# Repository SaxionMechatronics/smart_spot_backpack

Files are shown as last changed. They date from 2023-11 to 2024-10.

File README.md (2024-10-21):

# SMART SPOT Backpack

<p align="center" width="100%">
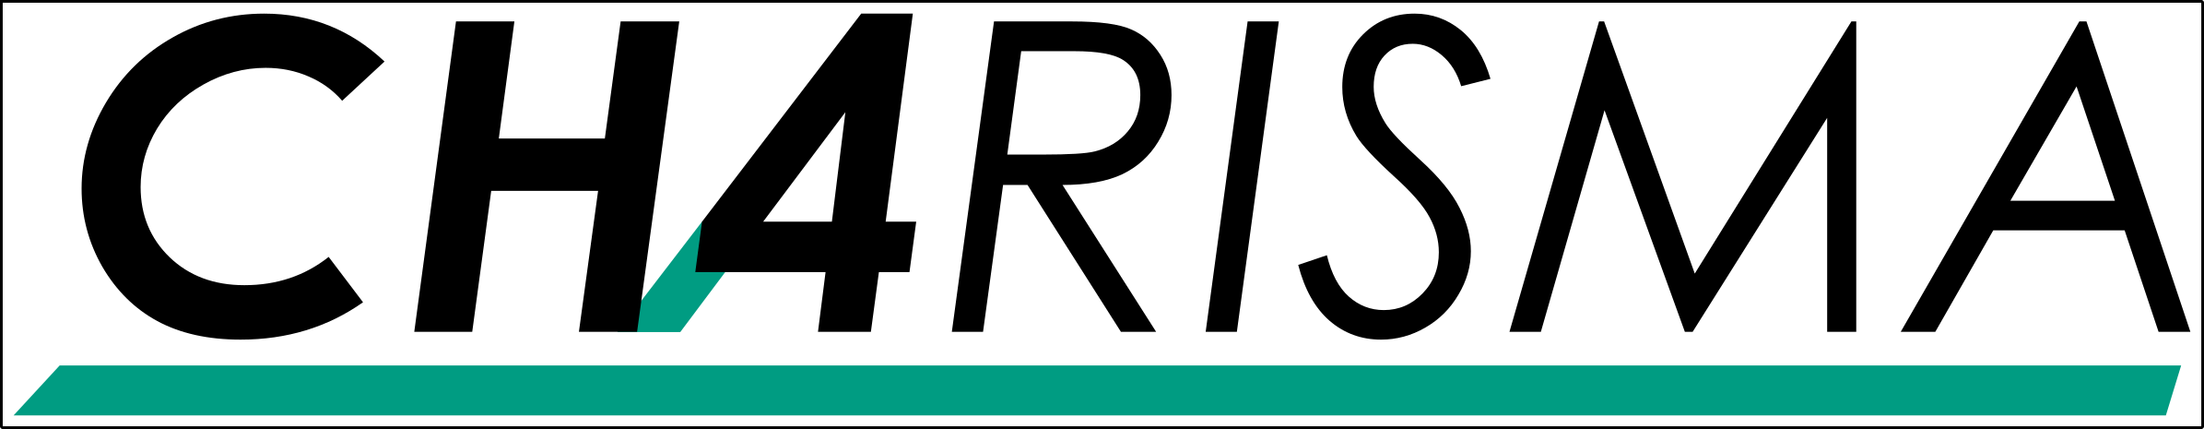
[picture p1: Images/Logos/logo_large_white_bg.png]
  
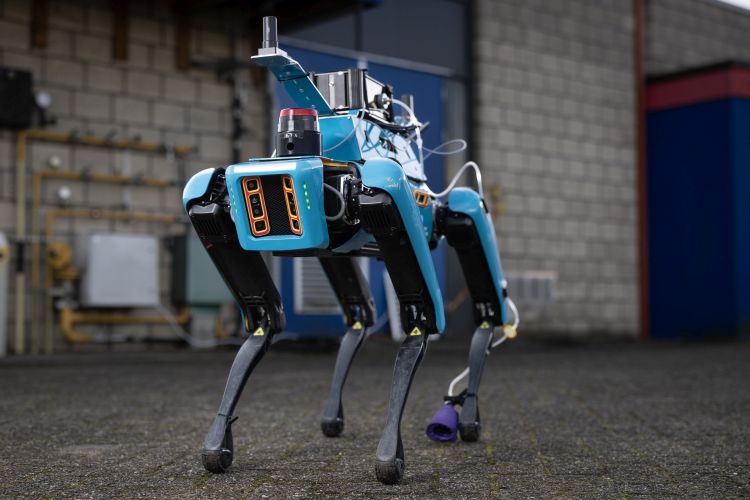
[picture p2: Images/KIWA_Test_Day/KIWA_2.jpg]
    
    <br>
    <em>SMART SPOT backpack being used in the CHARISMA project.</em>
</p>

This repository contains the SolidWorks files and documentation for the SMART SPOT Backpack: a backpack that has been developed for the Boston Dynamics robot [SPOT](https://bostondynamics.com/products/spot/) as part of the CHARISMA project of the [Smart Mechatronics And RoboTics (SMART) Research Group](https://www.saxion.edu/business-and-research/research/smart-industry/mechatronics) of the Saxion University of Applied Sciences. 

# Documentation
  * [A Word On Documentation](/Documentation/00-title.md)
  * [Context](/Documentation/01-context.md)
  * [Functional Overview](/Documentation/02-functional-overview.md)
  * [Quality Attributes](/Documentation/03-quality-attributes.md)
  * [Constraints](/Documentation/04-constraints.md)
  * [Requirements](/Documentation/xx-requirements.md)
  * [Principles](/Documentation/05-principles.md)
  * [Implementation](/Documentation/07-Implementation.md)
    * List of Parts 
    * Power Distribution
  * [Instructions](/Documentation/8-instructions.md)
    * [Manufacturing Instructions](/Documentation/8.1-manufacturing-instructions.md)
    * [Assembly Instructions](/Documentation/8.2-assembly-instructions.md)
    * [Mounting Instructions](/Documentation/8.3-mounting-instructions.md)
  * [Development Environment](/Documentation/12-development-environment.md)
  * [Support and Contributions](/Documentation/11-support-and-contributions.md)
  * [Architecture Decision Records](/Documentation/11-decision-log.md)
  * [Suggested Changes](/Documentation/12-Suggested-Changes.md)

# Specifications

| Parameter | Backpack V2.0.0 | 
| --- | --- |
| Weight | 3 kg |
| Dimensions | 20 x 40 x 10.5 cm|
| Material | Aluminium Sheet Metal |
| Voltage Outputs | 5, 12, 24 V (M12 Connectors) |
| Media Connectors | 4x USB 3.0, HDMI, Ethernet |
| On-board PC | VECOW SPC-7000|

# Directory Structure

```md
SPOT Backpack Repository                
├── CAD 
│   ├── 3D Drawings                     # .SLDPRT and .step files used in the assembly
|   |   ├── 3D Print Components
|   |   ├── Sheet Metal Components
|   |   ├── Other Components
│   |   └── Backpack Assembly.SLDASM    # Main assembly
│   └── Production Drawings             # Parts to be produced
|       ├── 3D Print Components         # .3MF files
|       └── Sheet Metal Components      # .step files for SOPHIA
├── Documentation
├── Images
└── Other Files                         
```

<p align="center">
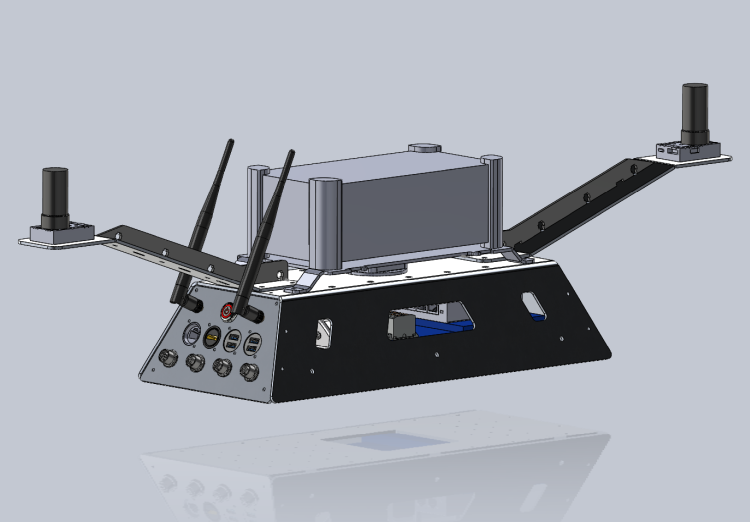
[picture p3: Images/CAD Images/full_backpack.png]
    
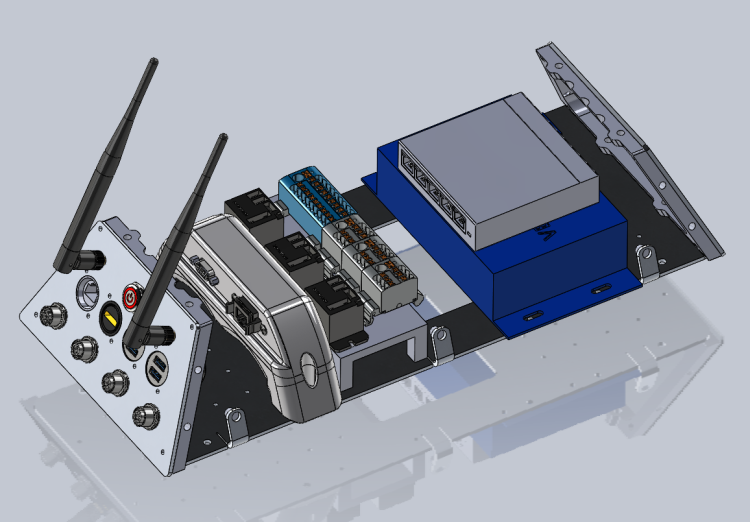
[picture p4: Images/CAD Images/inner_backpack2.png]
    
    <p align="center"><i>Solidworks assembly of the SMART SPOT Backpack.</i></p>
</p>

<p align="center" width="100%">
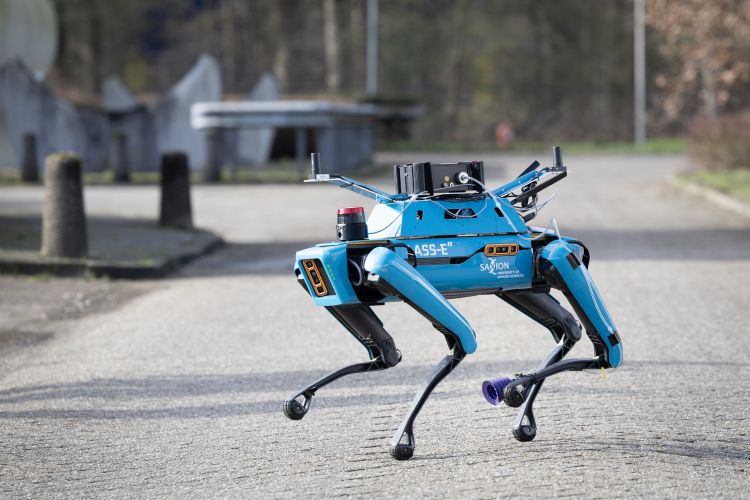
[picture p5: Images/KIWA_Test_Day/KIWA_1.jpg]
    
    <br>
    <em>SMART SPOT Backpack in action.</em>
</p>

## License
This project is released under the [CERN OHL v2 Weakly Reciprocal](https://choosealicense.com/licenses/cern-ohl-w-2.0/) license. Feel free to use, modify, and distribute the hardware designs in accordance with the terms of the license.

## Acknowledgments
This work from the SMART research group at Saxion University of Applied Sciences was supported by the Alliander Research Center for Digital Technologies and TechForFuture.

<p align="center" width="100">
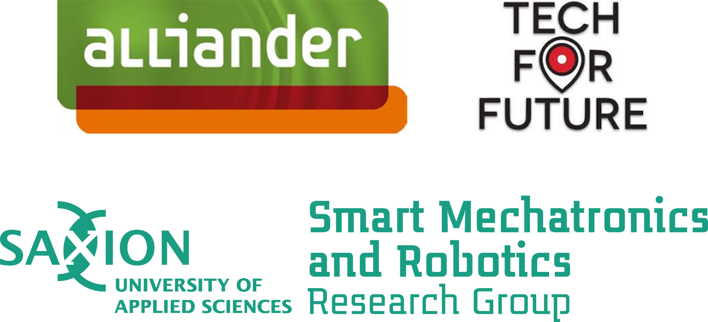
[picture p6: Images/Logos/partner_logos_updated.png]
    
</p>

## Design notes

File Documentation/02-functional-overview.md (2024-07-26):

## Functional Overview

This section gives a functional overview of the system as shown in figure 1: 

<p align="center" width="100%">
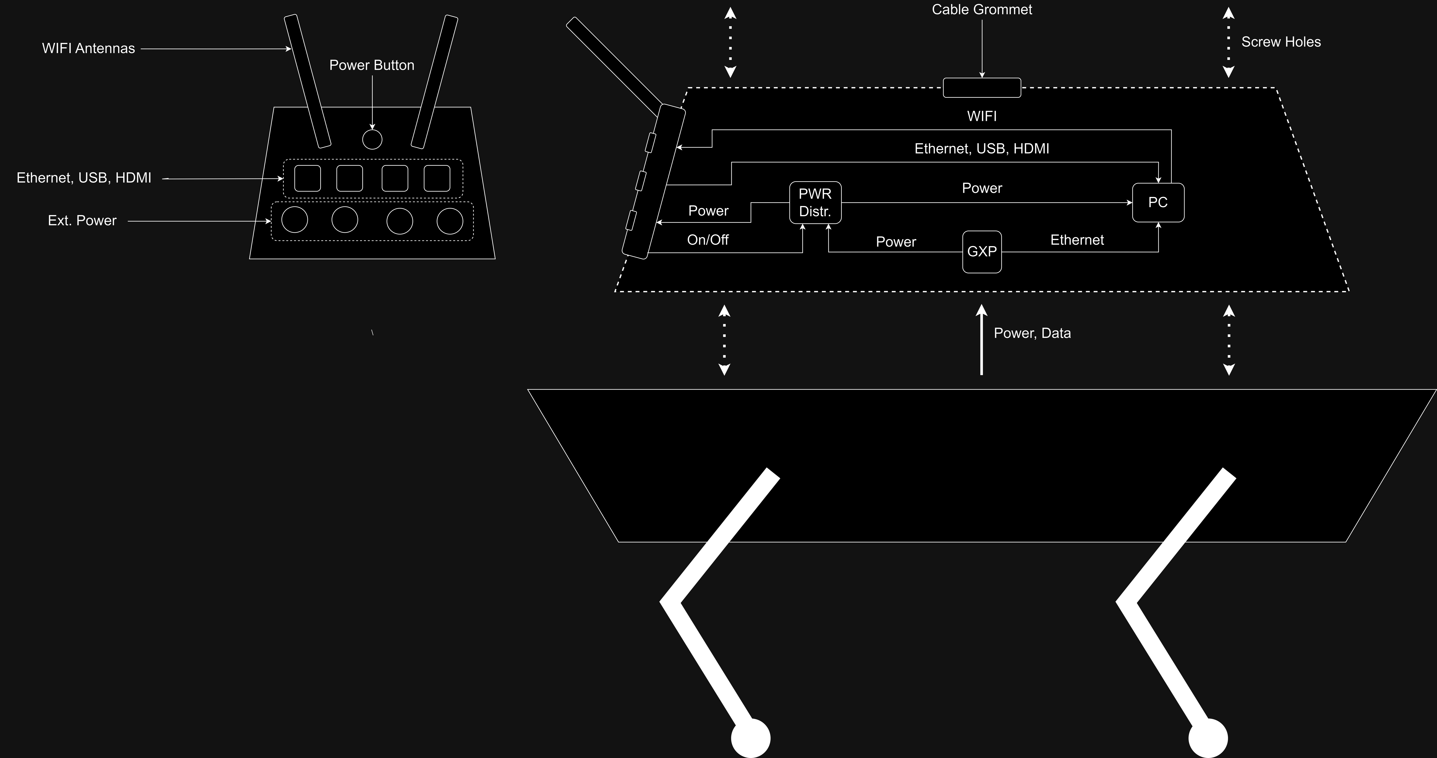
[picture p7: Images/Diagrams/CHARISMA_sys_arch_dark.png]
    
    <br>
    <em>Figure 1: Functional overview of the SPOT Backpack.</em>
</p>

In this diagram you can see that:
- The [General Expansion Payload (GXP)](https://support.bostondynamics.com/s/article/Spot-General-Expansion-Payload-GXP) provides power and data communication from SPOT 
- The power button bridges the power from the GXP to the power distribution
- Power is distributed via the power distribution (PWR Distr.) to the PC and to the interface panel
- The PC provides WIFI via 2 WIFI antennas
- The interface panel has various connectors that allow development with the on-board PC
- The top surface of the backpack includes a cable grommet and an array of screw holes

For a more in-depth electrical diagram, please see the [implementation](/Documentation/07-Implementation.md) section.

Below you can see a 3D version of the Backpack in SolidWorks (without any add-on components):

<p align="center">
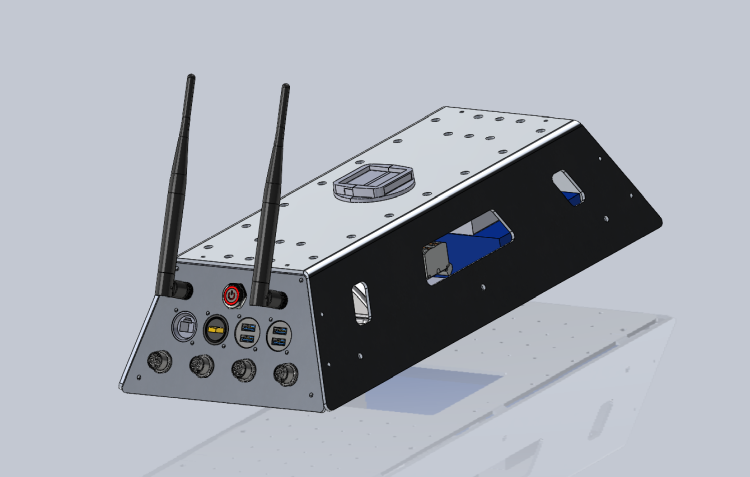
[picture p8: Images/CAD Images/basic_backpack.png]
    
    
    <p align="center"><i>SolidWorks assembly of the SMART SPOT Backpack.</i></p>
</p>

***

In the next section you can read about the key quality attributes that the system should satisfy.

> ➡️ [Next: Quality Attributes](./03-quality-attributes.md)

> ⬅️ [Previous: Context](./01-context.md)

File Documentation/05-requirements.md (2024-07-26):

## Requirements

This section describes the functional and technical requirements for the SPOT backpack. Requirements have been written based on [EARS](https://www.researchgate.net/publication/224079416_Easy_approach_to_requirements_syntax_EARS) and have been assigned a priority according to [MoSCoW](https://en.wikipedia.org/wiki/MoSCoW_method). 

*Keep in mind that these requirements have been written in context of the CHARISMA project.*

### Functional requirements

| Number | Requirement | Rationale | Priority |
| --- | --- | --- | --- |
| FR0101 | During normal operation of SPOT (i.e. walking, crouching, sitting, posing, walking stairs), the backpack shall not interfere with the motion of the robot. | We want a reliable backpack that does not interrupt basic operations of SPOT. | M | 
| FR0102 | When changing the battery while SPOT is laying on its side, the backpack shall not interfere. | If we change the battery, spot needs to be rolled over or on the side in order to access it. | M | 

### Technical requirements

#### Electric and electronic design

| Number | Requirement | Rationale | Priority |
| --- | --- | --- | --- |
| TR0101 | The backpack shall have clearly labelled cabling with rated voltages and current. | For maintenance reasons, it should be easy to understand the electrical wiring from just looking at it. | M | 
| TR0102 | The backpack shall provide one 24V, 12V and 5V external power connection each. | The bag pack should be able to cater the needs of various projects and their respective peripherals. | M | 
| TR0103 | The backpack shall provide different, standardized connectors for its external power connections that are labelled with rated voltages and current. | For safety reasons. For example, it should not be possible to connect a 5V to a 24V connection by accident. | M | 
| TR0104 | The backpack shall provide two WIFI antennas, one ethernet, one HDMI and four USB connections that are interfaced with its PC. | We want to easily develop on the PC of the bag pack. | M | 
| TR0105 | The backpack shall provide one power button that turns on/off its internals. | We want to power the PC and its peripherals only when needed. | M | 
| TR0106 | The power distribution of the backpack shall reserve 40W for the PC. | External devices that are powered via the 5V,12V or 24V connections should not be able to draw enough current to cut out the power to PC. The PC uses a maximum of 33.5W at peak conditions. | M | 

#### Mechanical design

| Number | Requirement | Rationale | Priority |
| --- | --- | --- | --- |
| TR0201 | The GNSS sensors of shall be located at the highest points of the backpack and not be occluded by any objects of the backpack. | Occlusions to the sky and reflections will disturb sensor readings. By placing the GNSS sensors at the highest point, we will get the best possible signal. | M | 
| TR0202 | The bag pack shall allow for a minimum distance of 80cm between the GNSS sensors. | There needs to be sufficient distance between the sensors to accurately determine the heading of the robot. | M | 
| TR0203 | The weight of the backpack shall be lower than 14.8 Kg where lower is better. | This is the maximum payload of SPOT. Reduced payload leads to reduced power consumption and thus longer operation times. | M | 
| TR0204 | The width of the backpack shall be at most 19 cm. | When the robot is not powered or walking stairs, the robot’s legs may move into the designated design space | M | 
| TR0205 | The length of the backpack shall be at most 85 cm. | Longer payloads will reduce maneuverability. | M | 
| TR0206 | The backpack shall have an IP rating of 0 where higher is better. | The backpack is built for research purposes only, it is therefore not required to have a higher IP rating. | M | 
| TR0207 | The backpack shall be made out of aluminum sheet metal. | Sheet metal parts are relative sturdy, cheap and easy to design. Additionally, they are easy to modify if needed  (e.g. drilling holes, filing). | S | 
| TR0208 | The backpack shall have only have screw holes with insert nuts (e.g. rivets nuts, heat inserts) on its outer shell. | 1) User friendliness: A user should be able to (un)-screw any object located on outer shell as easy as possible. 2) Reliability: The threading of tapped holes may deteriorate over time with repeated (un-)screwing. | S | 
| TR0209 | When (un-)mounting,  backpack shall require one tool, and two assembly steps. | User friendliness. It should be easy to (un)-mount the backpack to facilitate switching between different projects if needed. | S | 
| TR0210 | The  backpack shall require one disassembly step to access its internals. | Debugging and maintenance purposes. | S | 
| TR0211 | The backpack shall have only 3 and 5 mm screw holes. | This is to prevent confusion between screw hole sizes during assembly | S | 

***

In the next section you can read about the principles that have been used to design and build the backpack. 

> ➡️ [Next: Principles](./06-principles.md)

> ⬅️ [Previous: Constraints](./04-constraints.md)

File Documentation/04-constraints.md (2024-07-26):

## Constraints

This section states the constraints that affect the design of the backpack. The constraints and images w.r.t to SPOT are taken from the [Payload Developer Guide](https://dev.bostondynamics.com/docs/payload/payload_configuration_requirements.html) by Boston Dynamics and where applicable, further elaborated on.

Constraints include: 
- Mounting Surface
- Weight
- Dimensions
- Electrical Power and Data Interface to SPOT
- Manufacturing Guidelines of Sheet Metal Parts 

## Mounting Surface
The only mounting surface that SPOT provides are aluminum rails that are located along the left and right edges of the body. The rails accept T-slot nuts such as Misumi HNTR5-5. Mounting screws should not project more than 6.3mm below the top surface of the mounting rail.

<p align="center" width="100%">
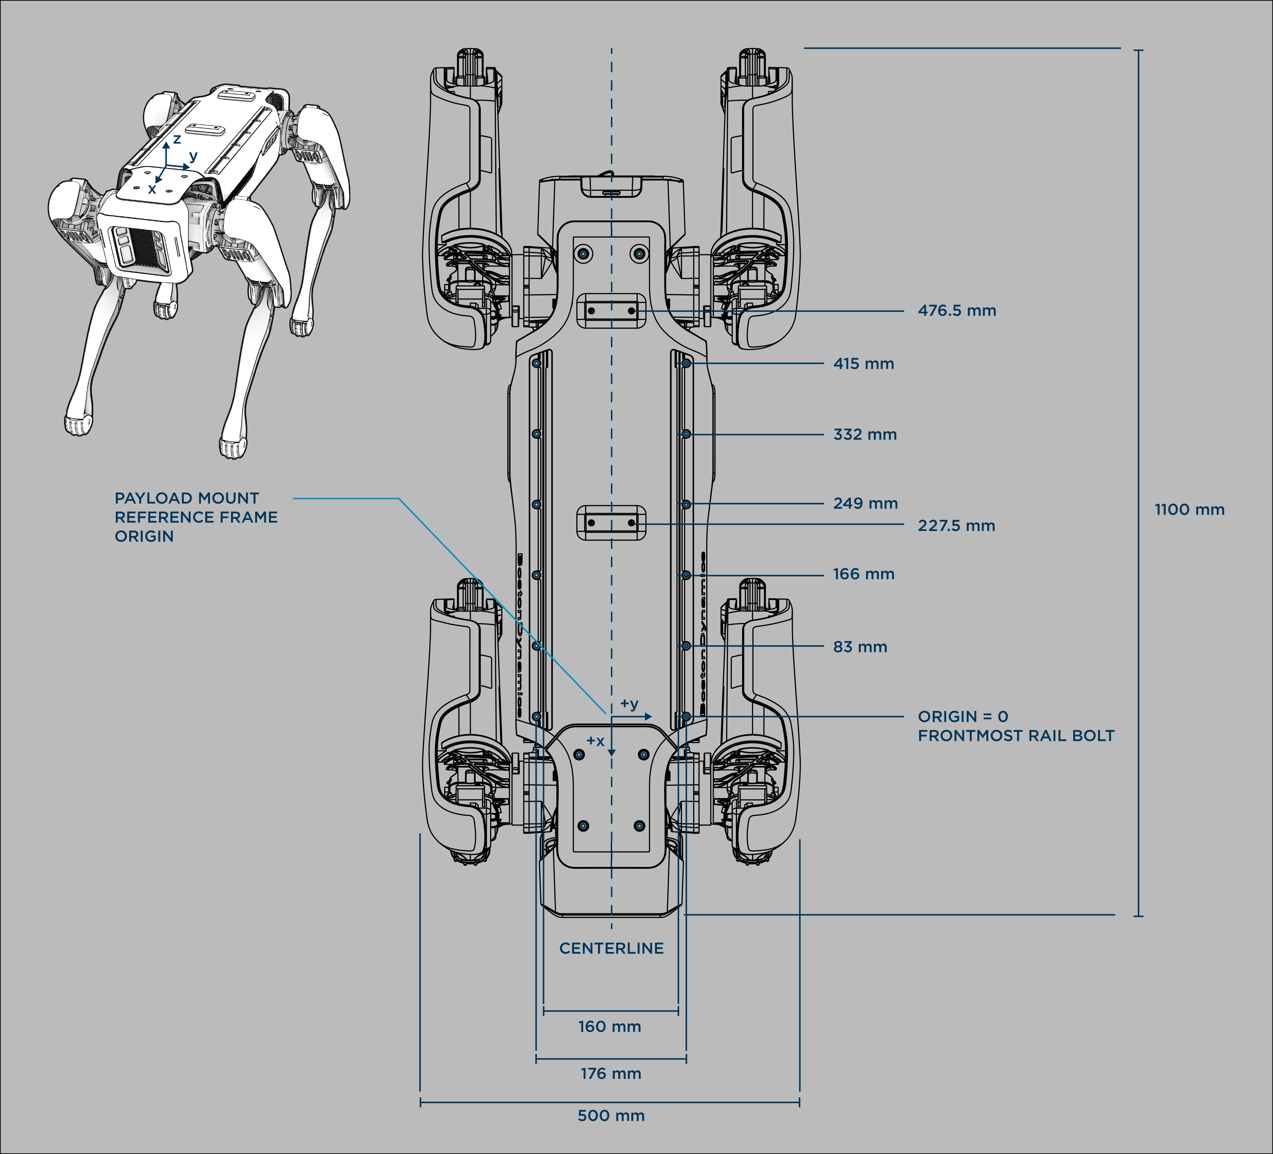
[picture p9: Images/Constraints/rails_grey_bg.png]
    
    <br>
    <em>Aluminum rails for mounting.</em>
</p>

<p align="center" width="100%">
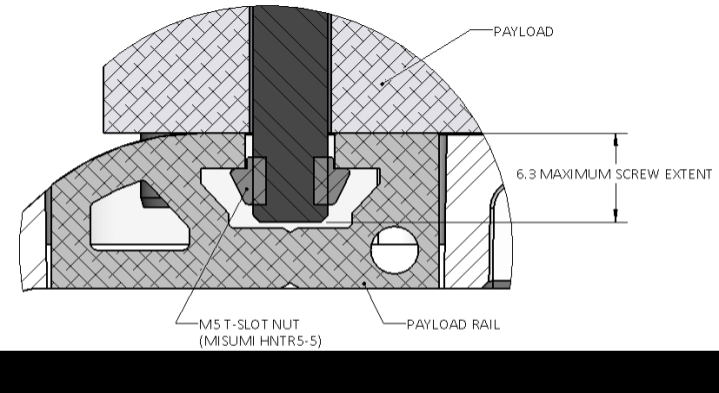
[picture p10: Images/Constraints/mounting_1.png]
    
    <br>
    <em>Mounting rail keying pin specifications in mm.</em>
</p>

## Payload Weight

SPOT has a maximum payload of 14.8 kg. Additionally, the weight of payload will also affect SPOT's battery consumption.
Furthermore, Spot can better handle payload mass if the combined center of mass lies between the front and rear hips. Spot will be more agile and less likely to fall if the total payload mass is centered on the middle of the robot.

## Payload Width
 
The maximum recommended width by Boston Dynamics for a body-mounted payload is 190mm. Wider payloads will result in reduced overall mobility and significant interference with the legs. 
For instance, SPOT's legs may shoot up when walking stairs or when self-righting.
One should thus avoid interference with the robot’s legs as shown below by avoiding the areas immediately adjacent to the robot’s hips.

<p align="center" width="100%">
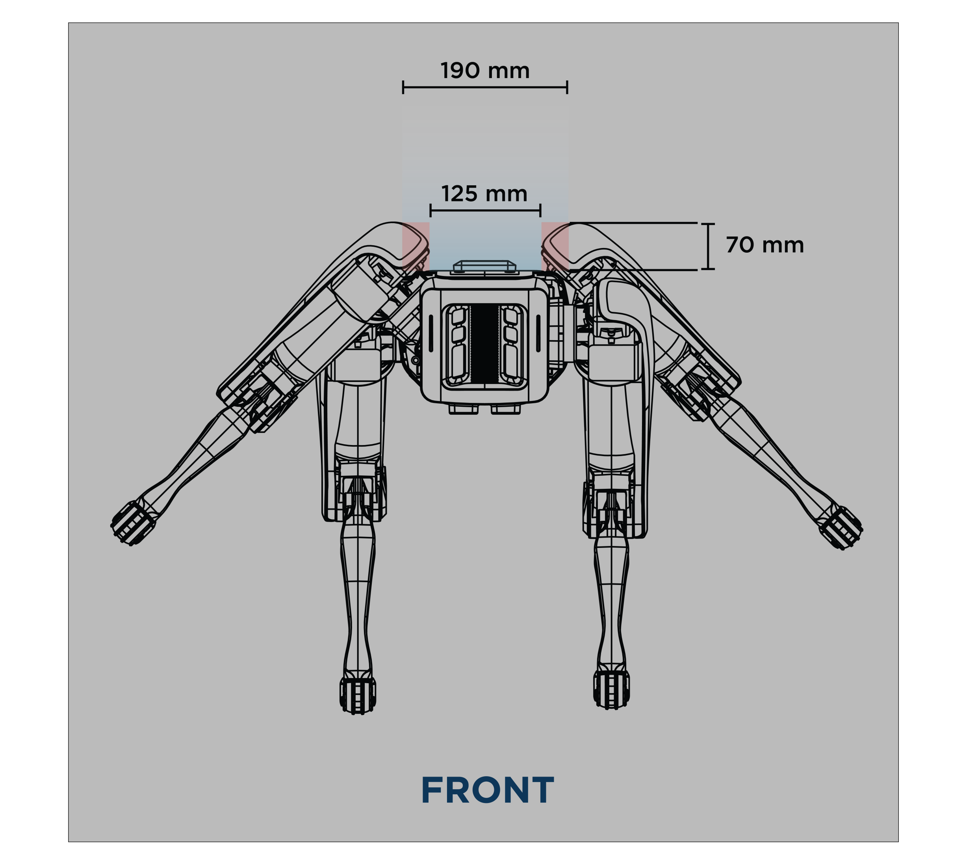
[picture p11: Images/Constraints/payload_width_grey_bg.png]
    
    <br>
    <em>Payload width constraint. Wider payloads may obstruct the leg movements of SPOT.</em>
</p>

## Payload Length
The payload should not overhang the front or rear of the robot as this will reduce maneuverability. For instance, when SPOT is standing in a corner or a narrow, it may not be able to turn around.

<p align="center" width="100%">
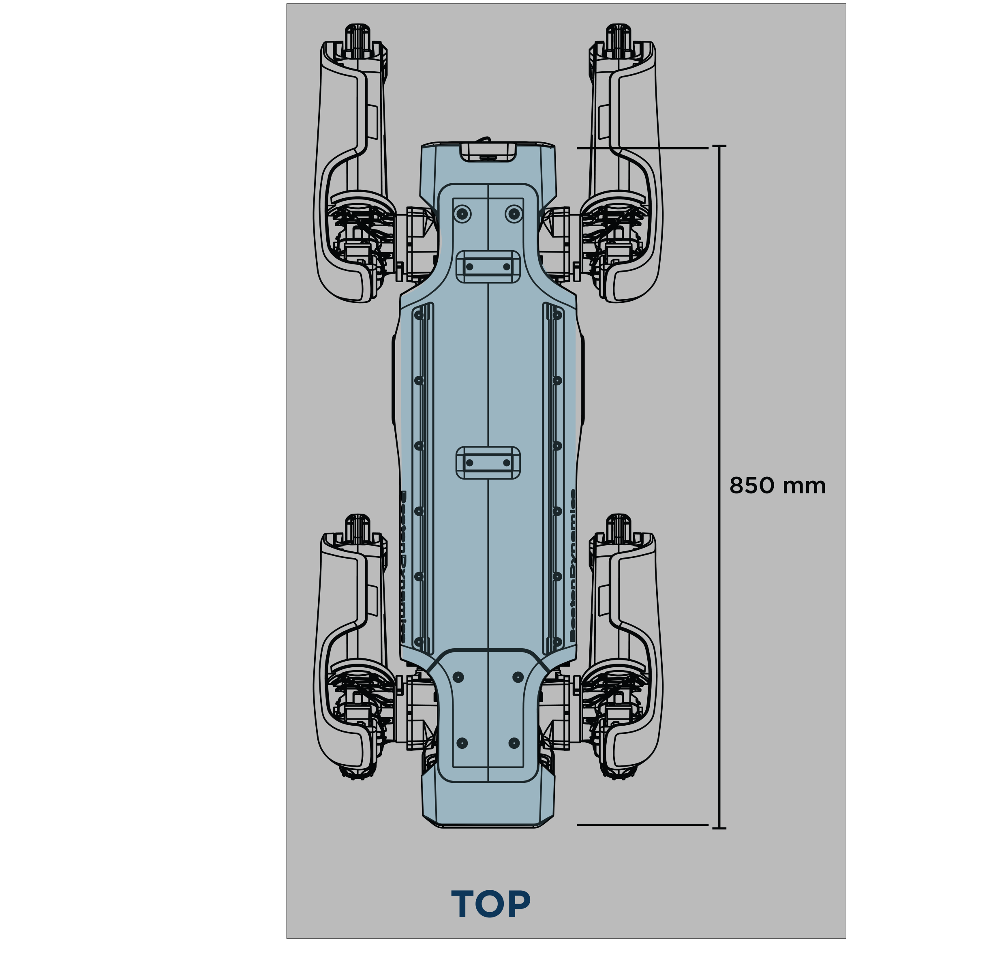
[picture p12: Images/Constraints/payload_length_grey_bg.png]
    
    <br>
    <em>Payload length constraint. Wider payloads may obstruct the turning radius SPOT.</em>
</p>

## Payload Height

The height of the payload impacts the robot’s ability to self-right and increases the height of the center of mass. Therefore, the center of mass low should be kept as low as possible, as the robot may not self-right if the payload is too top-heavy.

## Electrical Power and Data Interface (General Expansion Payload (GXP))

The [General Expansion Payload (GXP)](https://support.bostondynamics.com/s/article/Spot-General-Expansion-Payload-GXP) provides power and data communication to SPOT. 
Specifically, it provides a maximum of 150W shared between 12V and 24V, and 5V at a maximum of 10W via a HD15 connector. The pin out can be found on the documentation site of the GXP. Data communication is provided via a RJ45 connector.
In addition to the electrical constraints the GXP provides, it also exerts some mechanical constraints: 1), The GXP must fit inside the backpack and 2), the cable of the GXP must be connected to the payload connector on the top surface of SPOT, otherwise the [motors of SPOT will not start up](https://dev.bostondynamics.com/docs/payload/robot_electrical_interface).

## Sheet Metal Parts Manufacturing

Sheet metal parts have been manufactured via [247TailorSteel](https://www.247tailorsteel.com/en) which uses [SOPHIA](https://www.247tailorsteel.com/nl/sophia) as an online software tool for their manufacturing process. All sheet metal parts have to comply to their [manufacturing guidelines](https://www.247tailorsteel.com/en/service/submission-rules-and-guidelines), which include for example guidelines on cutting and bending of sheet metal parts.

***

In the next section you can read about the system requirements that gave rise to the design of the backpack.

> ➡️ [Next: Requirements](./05-requirements.md)

> ⬅️ [Previous: Quality Attributes](./03-quality-attributes.md)

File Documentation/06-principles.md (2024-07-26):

## Principles

This section summarizes the principles that have been used to design and build the backpack. 

### Lab usage
The backpack is designed to be used in (and outside) of the lab, not as a commercially available product.

### Poka Yoke
[Poka Yoke](https://en.wikipedia.org/wiki/Poka-yoke) (Mistake Proofing) Designing systems or products in a way that prevents errors or mistakes by users. 
For example, M12 connectors have been chosen with specific pinouts such that users cannot accidentally insert a 24V connection into a 5V connection.

### Rather buy than make it yourself
Rather buy products (like ethernet cables) than making them yourself. This is because it is cheaper (and usually more reliable) to order products than spending the time to make them yourself,

### Design for Assembly
DFA (Design for Assembly): Designing products with ease of assembly in mind to reduce assembly time, complexity, and costs. For example, 
  * Only use M3 & M5 screws with the same head in order to avoid confusion between screws and number of needed tools for assembly
  * Avoid having to use nuts by using threaded inserts
  * Mount for the gas sensor is designed such that battery straps can be easily removed

### Design for new add-ons
The backpack should have no high level constraints for new parts, in other words: it should be easy to design and integrate new parts for new projects. 

### Requirements Formulation
Requirements have been written based on [EARS](https://www.researchgate.net/publication/224079416_Easy_approach_to_requirements_syntax_EARS) and have been assigned a priority according to [MoSCoW](https://en.wikipedia.org/wiki/MoSCoW_method).

### Repository Maintenance  
Maintenance of the repository itself is based on [Gitflow](https://www.atlassian.com/git/tutorials/comparing-workflows/gitflow-workflow).

***

In the next section you can read about implementation details of the backpack, i.e. what parts have been used and how the power distribution has been designed.

> ➡️ [Next: Implementation](./07-Implementation.md)

> ⬅️ [Previous: Requirements](./05-requirements.md)

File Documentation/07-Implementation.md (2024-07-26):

## Implementation

This section describes the implementation details of this system. For this hardware project it includes a bill of materials and description of the power distribution.

### Bill of materials

You can find a bill of materials including costs and links to the respective products in `/Other Files`. Note that the list does not include tools and that some parts you may already have like the screws.

### Power Distribution

You can find a diagram of the power distribution below:

<p align="center" width="100%">
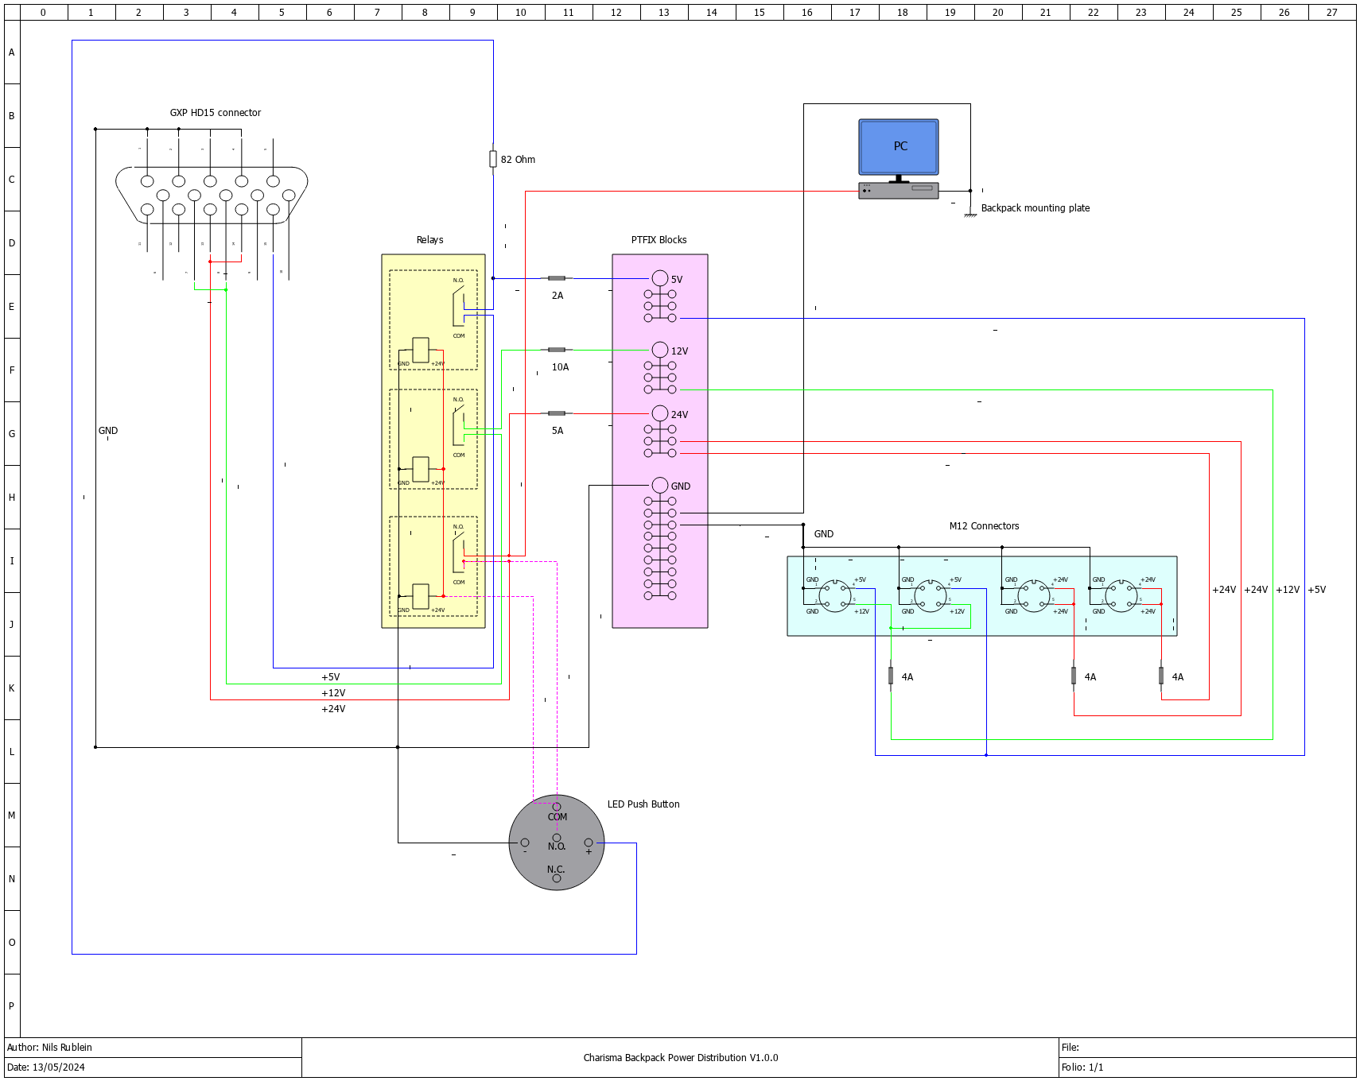
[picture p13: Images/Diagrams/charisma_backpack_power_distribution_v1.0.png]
    
    <br>
    <em>Electrical diagram of the power distribution.</em>
</p>

This file has been created using [QElectrotech](https://qelectrotech.org), which is free and works both on Linux and Windows. The corresponding `.qet` file can be found in `/Other Files`.

In the figure above you can see the following:

The GXP provides power and ground (GND) line to an array of [HF105F-4](https://nl.rs-online.com/web/p/power-relays/1218075) relays. A full pinout of the GXP can be found [here](https://support.bostondynamics.com/s/article/Spot-General-Expansion-Payload-GXP). The GXP provides 
* 12V and 24V shared at 150W
* 5V at 10W

The relays run at 24V and switch the connection from the Common (COM) port to the Normally Open (N.O.) port when the power button is pressed.
The 24V and the GND of the relays are connected in series for all three relays, which supply 24V, 12V and 5V respectively to a set of [PTFIX distribution blocks](https://www.phoenixcontact.com/en-pc/ptfix-distribution-blocks).

You can see a set of fuses (5A, 10A, 2A) between the relays and the PTFIX blocks. This is because we want to limit the power coming from the GXP to the power distribution for two reasons:

1) We do not know what kind of fuses are build into SPOT. If we draw too much power and a fuse breaks inside SPOT, we would have to wait for maintenance of Boston Dynamics. Therefore, we add our own fuses which we can easily replace ourselves.

2) If we draw too much power via external devices from the M12 connectors, there may be the chance that the PC does not get enough power and cuts out. In this case, the [Vecow 7000 SPC](https://www.vecow.com/dispPageBox/vecow/VecowCT.aspx?ddsPageID=PRODUCTDTL_EN&dbid=4739565050) uses between 17.7 and 33.5W depending on its CPU load. We  reserve thus (conservatively) 40W for the PC, by adding a 10A fuse to the 12V and a 5A fuse as the 24V line, as these lines share 150W. 

The amp ratings have been determined based on [this](https://peerlesselectronics.com/blog/choosing-right-fuse-for-your-needs.html) article:

**24V:** 

$110W / 24V = 4.6 A$ 

$4.6A * 1.25 = 5.75 A$

$(4.6A + 5.75A) / 2 ≈ 5 A$

**12V:** 

$110W / 12V = 9.2 A$

$9.2A * 1.25 = 11.5 A$

$(9.2A + 11.5A) / 2 ≈ 10 A$

**5V:**

$10W/2V = 2A$

$2A * 1.25 = 2.5A $

$(2A + 2.5A)/2 ≈ 2A$

Note that we use inline fuses due to space restrictions of the backpack. If more space would be available, mounted fuses (e.g. by PTFIX) would be the preferred choice.

Next, you can see that the PC is connected to the 24V PTFIX distribution block. The Vecow SPC 7000 runs anywhere between 9-55V, you may choose to connect it to the 12V instead. Additionally, you can see that the PC is grounded to the mounting plate of the backpack.

Finally, you can see a set of M12 connectors that supply 5V, 12V and 24V to external devices. Here, the connectors on the left provide 5V and 12V while the connectors on the right supply 24V. Note that the connectors on the left side have 4 poles and the connectors on the right have 5 poles. This is to avoid inserting a male M12 connector that should be connected to a 5V/12V connection, into a 24V connection. Finally, also here are fuses added at 4A, as the connectors are rated for 4A.

***

In the next section you can read about instructions on how to manufacture, assemble and mount the backpack.

> ➡️ [Next: Instructions](./8-instructions.md)

> ⬅️ [Previous: Principles](./06-principles.md)

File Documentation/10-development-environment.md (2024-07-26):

## Development Environment

The development environment section describes the used hardware and software tools to manufacture and assemble the backpack.

### Software Tools
* SOPHIA
* CURA (5.6.0)
* Solidworks 2023 (Only necessary if you want to (re)design parts)

### Hardware Tools
* 3D printer
* Rivet tool
* Soldering iron
* Crimp tool
* Wire stripper
* Allen key set
* Philips screwdriver
* Wrapping tools (Optional)
  
***

In the next section you can read the Architectural Decision Records, i.e. about decisions that a significant impact on the design of the backpack.

> ➡️ [Next: Architecural Decision Records](./11-decision-log.md)

> ⬅️ [Previous: Development Environment](./10-development-environment.md)

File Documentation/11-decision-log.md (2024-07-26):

## Architecture Decision Records 

In this section you can read the Architecture Decision Records (ADRs). 
For an introduction to ADRs, see [this](https://video.saxion.nl/media/Architecture+Design+Records+%28ADR%29+-+The+Basics/1_tbcapp6s) video.

Please note that ADRs are immutable. If you want to revert your decision, or change it, make a new ADR. As Michael Nygard put it:
> If a decision is reversed, we will keep the old one around, but mark it as superseded. (It's still relevant to know that it was the decision, but is no longer the decision.)

For new ADRs, you can find a template at the [bottom](#00x-template) of this page.

Decisions:
<!-- no toc -->
* [#003: Re-design version 1.0.0 such that the outer shell will be mounted on top of the mounting plate](#003-re-design-version-100-such-that-the-outershell-will-be-mounted-on-top-of-the-mounting-plate)
* [#002: The backpack will not be rainproof](#002-the-backpack-will-not-be-rainproof)
* [#001: We will design our own backpack](#001-we-will-design-our-own-backpack)

## #003: Re-design version 1.0.0 such that the outer shell will be mounted on top of the mounting plate
### Context
In [Version 1.0.0](https://bitbucket.org/mechatronica/spot_backpack_solidworks/src/1.0.0/), you had to slide in the mounting plate into the outer shell, however, you also needed to first connected the GXP. Finally, you also needed to connect the side panels, once the mounting plate was inside the outer shell.

Overall, our initial version was very cumbersome to install and not user-friendly at all.

### Decision
We will re-design version 1.0.0 such that the outer shell will be mounted on top of the mounting plate.

### Consequences
The consequence is that there is more time needed in development of the backpack. However, the backpack will be a lot more user-friendly w.r.t. to mounting and serviceability.

The alternative is to not redesign it, however this would lead to a lot of frustration when working with the backpack.

### Status
Accepted.

## #002: The backpack will not be rainproof
### Context
[Version 1.0.0](https://bitbucket.org/mechatronica/spot_backpack_solidworks/src/1.0.0/) of our backpack was made as a prototype to test if it is feasible to create our own backpack for our research group. This version was not rainproof.
During development of this backpack in the CHARISMA project, the question came up whether the backpack should be rainproof. For context, in the CHARISMA project we investigated automatic inspections of gas pipeline leakage, thus above ground and outdoors.

### Decision
The backpack will not be rainproof.

### Consequences
There are several consequences of this decision:
* It will be a lot easier to adjust [version 1.0.0](https://bitbucket.org/mechatronica/spot_backpack_solidworks/src/1.0.0/) for further development.
* We still comply with Dutch norms for gas pipeline leakage inspections. Specifically, [NEN7249](https://www.nen.nl/en/nen-7249-2020-nl-272894) forbids inspection with carpet probes during rain, as rain compromises the measurements.
* Other future projects in our research group may not be able to use the backpack if it is not rainproof. However, generally we design our systems not to be rainproof as our research group focuses on TRL levels [4-7] and we usually only conduct outdoor tests on days where it is not raining. Thus, this is most likely not an issue for our research group. 

The alternative  was to redesign our first prototype to be rainproof. However, this would have required a lot more effort for designing and testing, which was not feasible given the available time back then during the CHARISMA project.

### Status
Accepted.

## #001: We will design our own backpack

### Context
When we started the CHARISMA project we already had a prototype backpack from Clearpath Robotics at our lab, however the mounting spots on the backpack were limited and the backpack itself was very cumbersome to mount and service. With these issues and some other reasons we wanted to know if it is feasible to make some adjustments on the current backpack or make a completely new one. 

### Decision
We are going to design our own backpack.

### Consequences
The consequence of this decision is that we have to spend a good amount of time in making the backpack, that is: designing, manufacturing, assembling and testing.

There are two alternatives to this decision:
1. Keep using the Clearpath Robotics backpack and adjust it to our needs. However, the consequence of this is that also for future projects we will run into the same problems (serviceability, mounting options, etc.)
2. Buy a different backpack. However, at the time of this decision (~ September 2023), there did not seem to be viable options on the market to replace the current backpack and make it fit for our use case.

### Status
Accepted.

## #000: Template

### Context
*What is the issue that we're seeing that is motivating this decision or change?*

### Decision
*What is the change that we're proposing and/or doing?*

### Consequences
*What becomes easier or more difficult to do because of this change?*

### Status
*What is the status, such as proposed, accepted, rejected, deprecated, superseded, etc.?*

***

In the next section you can read about suggested changes to improve the design of the backpack.

> ➡️ [Next: Suggested Changes](./12-Suggested-Changes.md)

> ⬅️ [Previous: Development Environment](./10-development-environment.md)

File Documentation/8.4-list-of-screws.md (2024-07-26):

# Screws

This document keeps track of the different screws used for the backpack. The section base refers to everything that you need in you case just want to mount the backpack without anything project related.
The section "Auxillary: CHARISMA" here refers to auxiliary equipment and the necessary screws for this equipment. 

Feel free to add the screws for any other auxillary equipment.

## Base

### Interface Panel
* 8x M3x10 (2x bottom, 2x top, 4x front)
* 8x M3x12 (For media connectors, e.g. USB)
* 8x M3 nuts

### Front Panel
* 8x M3x10 (2x bottom, 2x top, 4x front)

### GXP
* 2x M5x20 
* 2x M5 nuts

### PWR DISTR
* 12x M3x8 (6x relays + 2x DIN rail + 4x mounting plate)
* 2x M3 washers

### PC
* 2x M3x8
* 2x M3 nuts
* 2x M3washers

### Outer Shell
* 4x M5x16

### Base plate plate
* 4x M5x12 

## Auxillary: CHARISMA

### Laser Hunter mount
* 4x M5x16

### GNSS wings
* 8x M5x16
* 6x M5x12 
* 4x M5x20
* 6x M2.5x8
* 10x M5 nuts

***

In the next section you can read about how you can contribute and how we can support you.

> ➡️ [Next: Support & Contributions](./9-support-and-contributions.md)

> ⬅️ [Previous: Mounting Instructions](./8.3-mounting-instructions.md)

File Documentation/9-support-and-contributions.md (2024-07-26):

## Support and Contributions

The operations and support section describes to what extent we provide support and how people can contribute to this project.

### Support
We do not provide any support for this project. However, you can always reach out to our research group if you have any questions by sending a mail to `secretariaat.smart.led@saxion.nl`.

### Contributions
You may contribute by developing a modification or feature to the backpack and making a pull request. 

***

In the next section you can read about what kind of software and hardware tools you need to design and build the backpack.

> ➡️ [Next: Development Environment](./10-development-environment.md)

> ⬅️ [Previous: List of screws](./8.4-list-of-screws.md)

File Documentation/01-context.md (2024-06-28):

## Context

This is the open source hardware repository for the [Boston Dynamics SPOT](https://bostondynamics.com/products/spot/) backpack from the [Smart Mechatronics And RoboTics (SMART) research group](https://www.saxion.edu/business-and-research/research/smart-industry/mechatronics) of the Saxion University of Applied Sciences.

The development of this backpack was driven by a commercial model previously used within our research group, which was difficult to modify for the needs of our projects.

The backpack has been developed within the CHARISMA project and is now released as open source hardware repository to be used by researchers as a developing platform for SPOT. 
As such, the backpack the contains it's own onboard PC, power distribution system, various power and media connectors as well as an array of screw holes on the top surface for mounting additional payloads such as sensors and actuators.

<p align="center" width="100%">
    
    <br>
    <em>SPOT backpack being used in the CHARISMA project at the KIWA test site in Apeldoorn.</em>
</p>

***
In the next section you read about functional overview of the system in which the functions and interfaces of the system are explained.

> ➡️ [Next: Functional Overview](./02-functional-overview.md)

> ⬅️ [Previous: A word on documentation](./01-context.md)

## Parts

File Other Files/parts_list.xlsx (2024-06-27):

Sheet: Sheet1
Amount | Unit | Product Description | Website | Article Number | Excluding VAT | Including VAT | Excl. VAT / unit | Total incl. VAT | Remarks
Conrad
2 | piece | SACC-E-M12FS-5CON-PG9/1,0 VAPO | https://www.conrad.be/nl/p/phoenix-contact-1671098-sensor-actuator-steekconnector-m12-aantal-polen-5-bus-inbouw-0-50-m-1-stuk-s-748077.html | 748077 – 62 | 11.8421 | 14.99 | 23.6842 | 29.98 | Update new M12 connectors
2 | piece | SACC-E-M12FS-4CON-PG9/1,0 VAPO | https://www.conrad.be/nl/p/phoenix-contact-1693788-sensor-actuator-steekconnector-m12-aantal-polen-4-bus-inbouw-0-50-m-1-stuk-s-748052.html | 748052 – 62 | 11.8421 | 14.99 | 23.6842 | 29.98
1 | set | Phoenix Contact PTFIX 6/18X2,5-NS35 BK | https://www.conrad.be/nl/p/phoenix-contact-ptfix-6-18x2-5-ns35a-bk-3273256-verdeelblok-0-14-mm-2-50-mm-zwart-8-stuk-s-1831596.html | 1831596 – 62 | 61.6121 | 77.99 | 61.6121 | 77.99
1 | set | Phoenix Contact PTFIX 6/6X2,5-NS35A RD | https://www.conrad.be/nl/p/phoenix-contact-ptfix-6-6x2-5-ns35a-rd-3273202-verdeelblok-0-14-mm-2-50-mm-rood-10-stuk-s-1831578.html | 1831578 – 62 | 36.3321 | 45.99 | 36.3321 | 45.99
1 | set | Phoenix Contact PTFIX 6/6X2,5-NS35A GY | https://www.conrad.be/nl/p/phoenix-contact-ptfix-6-6x2-5-ns35a-gy-3273198-verdeelblok-0-14-mm-2-50-mm-grijs-10-stuk-s-1831577.html | 1831577 – 62 | 36.3321 | 45.99 | 36.3321 | 45.99
1 | set | Phoenix Contact PTFIX 6/6X2,5-NS35A BU | https://www.conrad.nl/nl/p/phoenix-contact-ptfix-6-6x2-5-ns35a-bu-3273200-verdeelblok-aantal-polen-7-0-14-mm-2-5-mm-blauw-10-stuk-s-1563500.html | 1563500 – 62 | 35.5421 | 44.99 | 35.5421 | 44.99
4 | piece | Phoenix Contact 1662528 Sensor/actuator connector | https://www.conrad.be/nl/p/phoenix-contact-1662528-sensor-actuator-connector-niet-geassembleerd-m12-aantal-polen-4-stekker-recht-1-stuk-s-748793.html | 748793 - 62 | 11.8421 | 14.99 | 47.3684 | 59.96
4 | piece | Phoenix Contact 1663116 Sensor/actuator connector, niet geassembleerd M12 Aantal polen: 5 Stekker, recht 1 stuk(s) | https://www.conrad.be/nl/p/phoenix-contact-1663116-sensor-actuator-connector-niet-geassembleerd-m12-aantal-polen-5-stekker-recht-1-stuk-s-748817.html | 748817 - 62 | 13.4221 | 16.99 | 53.6884 | 67.96 | Check if new M12 connectors also have PG9
4 | piece | Phoenix Contact 1504084 Sensor/actuator connector, toebehoren PG9 Contramoer 1 stuk(s) | https://www.conrad.be/nl/p/phoenix-contact-1504084-sensor-actuator-connector-toebehoren-pg9-contramoer-1-stuk-s-746878.html | 746878 - 62 | 1.1771 | 1.49 | 4.7084 | 5.96 | Update new M12 connectors also have PG9
247 Taylor Steel
1 |  | Backpack sheet metal parts | https://sophia.247tailorsteel.com/ |  | 201.9 | 244.299 | 201.9 | 244.299 | Price may differ depending on how many parts you order. This quote of this order included some backup parts as well parts specific to the CHARISMA project, which may not be needed for your project.
1 |  | Packaging |  |  | 6.25 | 7.5625 | 6.25 | 7.5625
1 |  | Shipping |  |  | 9.6 | 11.616 | 9.6 | 11.616
TessaTronics
2 | piece | QIANRENON Dual USB 3.0 Panel Mount Connector, USB 3.0 Vrouwelijke naar Vrouwelijke Koppeling Socket Panel Mount Pass Through Adapter, Vaste Panel Voor en Achter Rechte USB Extender | https://www.amazon.nl/QIANRENON-Connector-Vrouwelijke-Koppeling-Extender/dp/B09FL99YL6 | B09FL99YL6 | 15.0021 | 18.99 | 30.0042 | 37.98 | No delivery costs for Amazon since the order is above 20 euros.
1 | set | KEL-BES-S 50 zwart Borstelplaat voor Kabeldoorvoer+moer | https://www.ccned.nl/nl/icotek-51540 | 51540 | 63.27 | 76.5567 | 63.27 | 76.5567
1 |  | Delivery costs (ccned) |  |  | 11.85 | 15 | 11.85 | 15
1 | piece | GXP | https://www.robotlab.com/store/-ports |  | 1181.21 | 1429.2641 | 1181.21 | 1429.2641 | NOTE: This site is out of date! Probably best to contact Boston Dynamics directly and ask for a quote / vendor!
2 | piece | WIFI antenna (Female RP-SMA) | https://www.allekabels.nl/wifi-router-antenne/1761/1084927/wifi-antenne-5-dbi.html | 1084927 | 10.0251 | 12.69 | 20.0502 | 25.38
2 | piece | RP-SMA (male) - RP-SMA (female) cable | https://www.onlinekabOKS-06332elshop.nl/rp-sma-m-rp-sma-v-verlengkabel-1-meter.html?gad_source=1 | OKS-06332 | 3.1521 | 3.99 | 6.3042 | 7.98
1 | piece | DIN rail | https://www.elektramat.nl/jmv-ts35-f5-din-rail-per-2-meter-ts35-f5/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 | 401013476 | 5.0876 | 6.44 | 5.0876 | 6.44
1 | piece | LED power button 16mm | https://www.tinytronics002901.nl/en/switches/manual-switches/push-buttons-and-switches/metal-push-button-16mm-on-off-with-3v-white-led-lighting | "002901" | 2.765 | 3.5 | 2.765 | 3.5
4 | piece | USB A (male) - USB A (male) cable 0.3m | https://www.onlinekabelshop.nl/usb-naar-usb-kabel-usb3-0-tot-2a-zwart-0-30-meter.html?gad_source=1 | OKS-32009 | 6.1541 | 7.79 | 24.6164 | 31.16
10 | piece | Misumi Insertion Lock Nut HNTR5-5 | https://uk.misumi-ec.com/vona2/detail/110302247820/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 | HNTR5-5 | 0.61 | 0.7381 | 6.1 | 7.381 | Not clear if with or without VAT
RS Components
1 | bag | POP Steel Tubular Rivet, 6.9mm | https://nl.rs-online.com/web/p/rivets/7689962?gb=s | 768-9962 | 18.2411 | 23.09 | 18.2411 | 23.09 | There are no delivery costs since the orders are combined over 75 euros.
3 | piece | Hongfa Europe GMBH Flange Mount Power Relay, 24V dc Coil, 20A Switching Current, SPDT | https://nl.rs-online.com/web/p/power-relays/1218075 | 121-8075 | 6.9915 | 8.85 | 20.9745 | 26.55
1 | piece | Littelfuse Automotive Fuse Kit (ATO size) | https://nl.rs-online.com/web/p/fuse-kits/2199556 | 219-9556 | 45.5988 | 57.72 | 45.5988 | 57.72
1 | bag | M3 Brass Threaded Insert | https://nl.rs-online.com/web/p/threaded-inserts/2040616 | 204-0616 | 15.8553 | 20.07 | 15.8553 | 20.07
1 | piece | 0.5 ethernet cable | RS PRO Cat6 Male RJ45 to Male RJ45 Ethernet Cable, S/FTP, Black PVC Sheath, 0.5m | 411-384 | 3.23 | 3.9083 | 3.23 | 3.9083
1 | bag | M3 x 10mm | https://nl.rs-online.com/web/p/socket-screws/6604636?gb=s | 660-4636 | 27.255 | 34.5 | 27.255 | 34.5 | Buying these screws seperately seems slightly cheaper than buying a torque screw kit, like https://nl.rs-online.com/web/p/screw-bolt-kits/2253363?gb=s
1 | bag | M3 x 12mm | https://nl.rs-online.com/web/p/socket-screws/0281007?gb=s | 281-007 | 17.933 | 22.7 | 17.933 | 22.7
1 | bag | M3 x 8mm | https://nl.rs-online.com/web/p/socket-screws/0280997?gb=s | 280-997 | 18.8968 | 23.92 | 18.8968 | 23.92
1 | bag | M5 x 20mm | https://nl.rs-online.com/web/p/socket-screws/0281091?gb=s | 281-091 | 19.4498 | 24.62 | 19.4498 | 24.62
1 | bag | M5 x 16mm | https://nl.rs-online.com/web/p/socket-screws/0281085?gb=s | 281-085 | 21.3616 | 27.04 | 21.3616 | 27.04
1 | bag | M5 x 12mm | https://nl.rs-online.com/web/p/socket-screws/0281079?gb=s | 281-079 | 21.6065 | 27.35 | 21.6065 | 27.35
1 | bag | M5 nuts | https://nl.rs-online.com/web/p/hex-nuts/0189585?gb=s | 189-585 | 10.4754 | 13.26 | 10.4754 | 13.26
1 | bag | M3 nuts | https://nl.rs-online.com/web/p/hex-nuts/0189563?gb=s | 189-563 | 7.3707 | 9.33 | 7.3707 | 9.33
Farnell
1 | piece | CLIFF ELECTRONIC COMPONENTS CP30220 | https://nl.farnell.com/en-NL/cliff-electronic-components/cp30220/utp-adaptor-rj45-jack-8p8c-cat5e/dp/2491569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 | 2491569 | 6.54 | 7.9134 | 6.54 | 7.9134
1 | piece | NEUTRIK NAHDMI-W-B | https://nl.farnell.com/neutrik/nahdmi-w-b/adaptor-hdmi-feedthrough-panel/dp/1713532 | 1713532 | 13.9593 | 17.67 | 13.9593 | 17.67
5 | piece | LITTELFUSE 277.6306.0001 | https://nl.farnell.com/littelfuse/277-6306-0001/fuse-holder-in-line-blade/dp/310505 | 310505 | 8.0264 | 10.16 | 40.132 | 50.8
1 | piece | PRO SIGNAL PSG91580 | https://nl.farnell.com/pro-signal/psg91580/lead-displayport-hdmi-male-male/dp/3403404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 | 3403404 | 4.81 | 5.8201 | 4.81 | 5.8201 | This cable is specific to the PC we used (VECOW SPC7000) which had displayports. Only order this if your PC also uses displayports instead of HDMI, e.g. https://nl.rs-online.com/web/p/hdmi-cables/1765697?gb=s
1 | piece | HD 15 connector | https://nl.farnell.com/amphenol-icc-commercial-products/l17d45pk-p-09-l717hde15p/hd-d-sub-connector-plug-15pos/dp/2920966 | 2920966 | €2.82 | 3.4122 | 2.82 | 3.4122 | Check length. Alternatively, this one would be better for assembly, however protbably too long: https://ampul.eu/en/connectors/4920-d-sub-de15-db15-cable-connector-male-with-nuts-scr
 |  |  |  |  |  | Total | 2208.4694 | 2712.5933

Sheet: PARAMS
Supplier label | Supplier | Multiplier | VAT
TessaTronic (8%) | TessaTronic | 1.08 | 21%
TessaTronic (15%) | TessaTronic | 1.15
TessaTronic (25%) | TessaTronic | 1.25

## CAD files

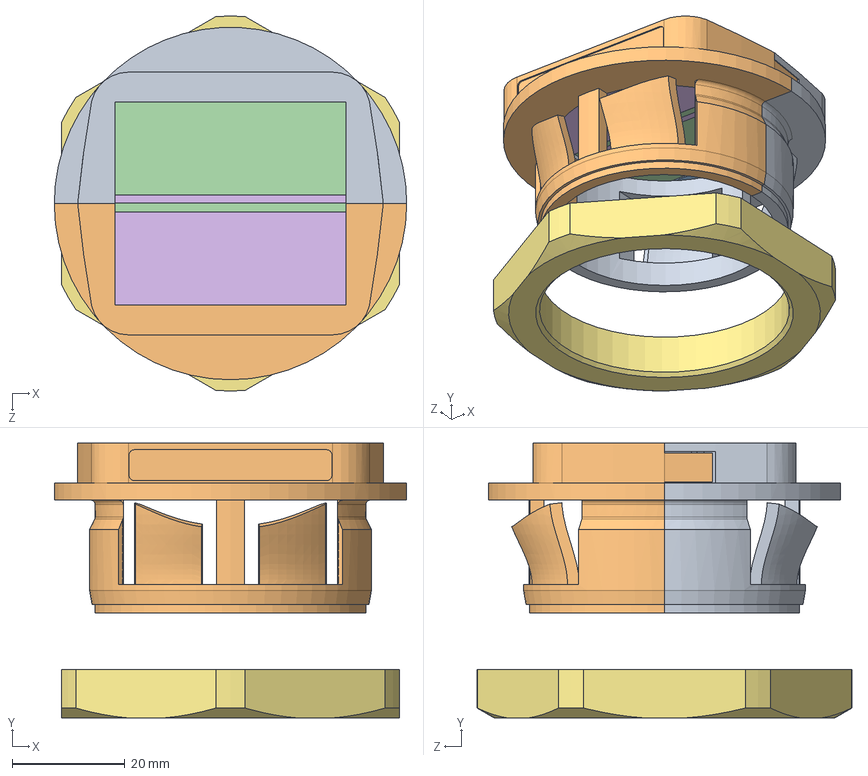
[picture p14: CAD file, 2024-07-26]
CAD/01. 3D_Drawings/03. Other_Components/Cable Grommet/Cable Grommet.SLDASM
62.5 x 48.7 x 66.5 mm

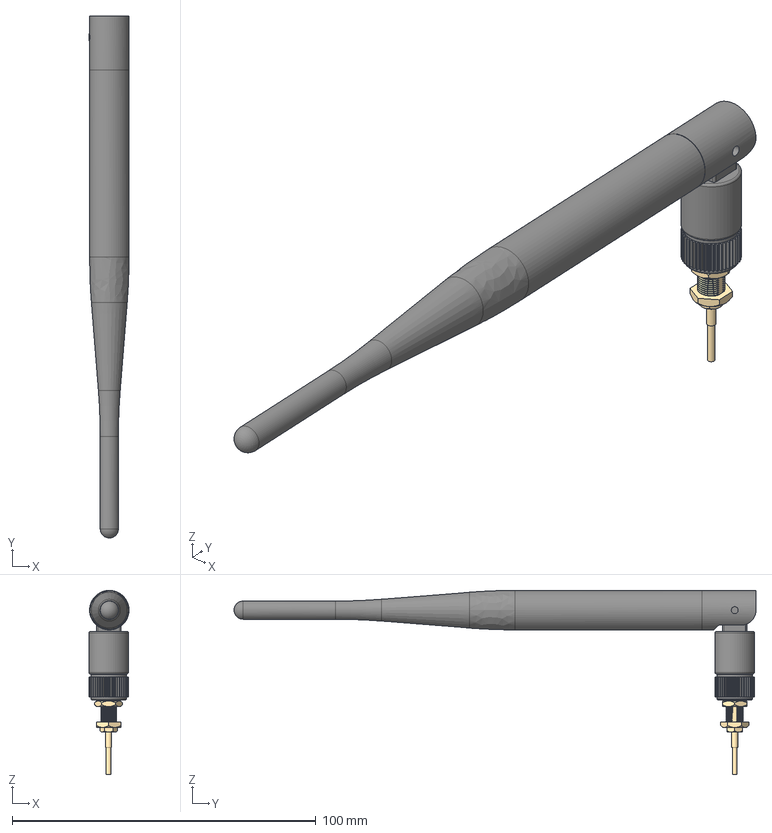
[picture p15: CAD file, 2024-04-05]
CAD/01. 3D_Drawings/03. Other_Components/panel_components/wifi-antenna-9.snapshot.2/Antenna_assembly v4.step
13.2 x 171.8 x 60.6 mm
antenna_part_2
antenna_part_1
antenna_part_3
SMA_connector_part_1
SMA_connector_part_2

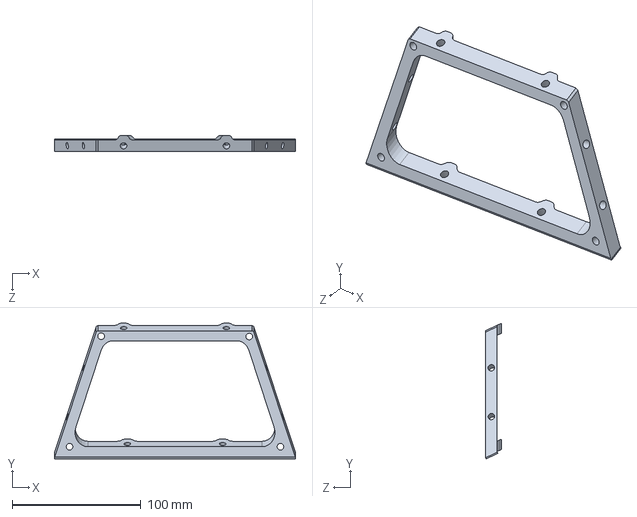
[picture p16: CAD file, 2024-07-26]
CAD/01. 3D_Drawings/01. 3D_Print_Components/Bracket.SLDPRT
187.4 x 105.5 x 12.7 mm

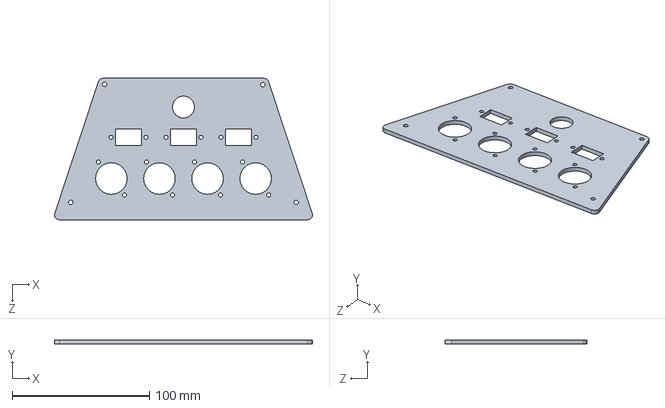
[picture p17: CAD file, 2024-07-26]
CAD/01. 3D_Drawings/02. Sheet_Metal_Components/Panel Front.SLDPRT
187.7 x 3.00 x 103.0 mm

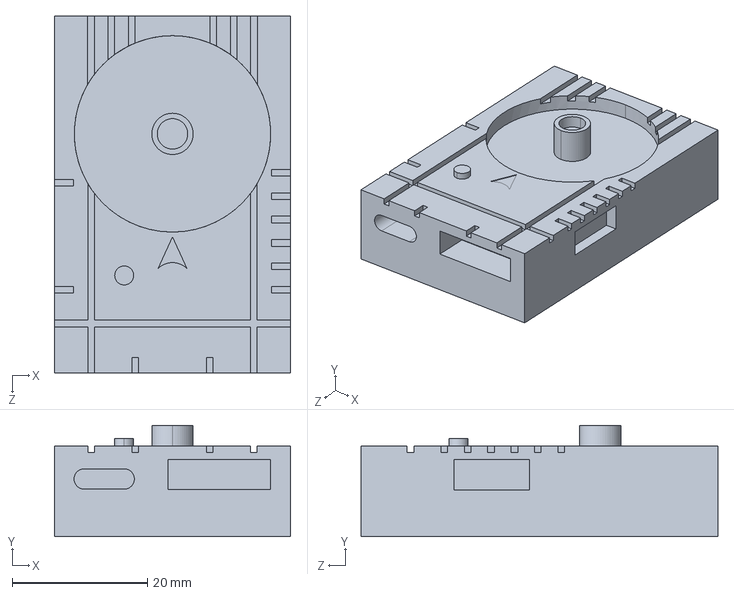
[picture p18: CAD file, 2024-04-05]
CAD/01. 3D_Drawings/03. Other_Components/H-RTK F9P HNSS/H-RTK F9P GNSS Helical.STEP
34.9 x 16.4 x 52.7 mm

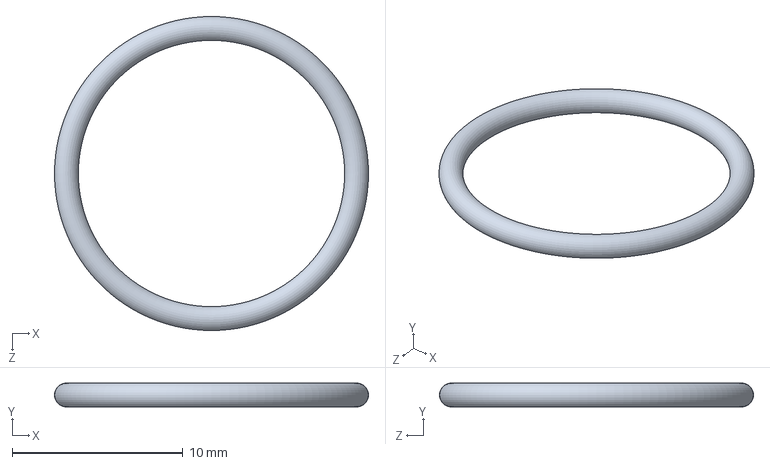
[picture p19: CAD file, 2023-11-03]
CAD/01. 3D_Drawings/03. Other_Components/panel_components/LED_Button16mm/O-Ring.SLDPRT
18.4 x 1.39 x 18.4 mm

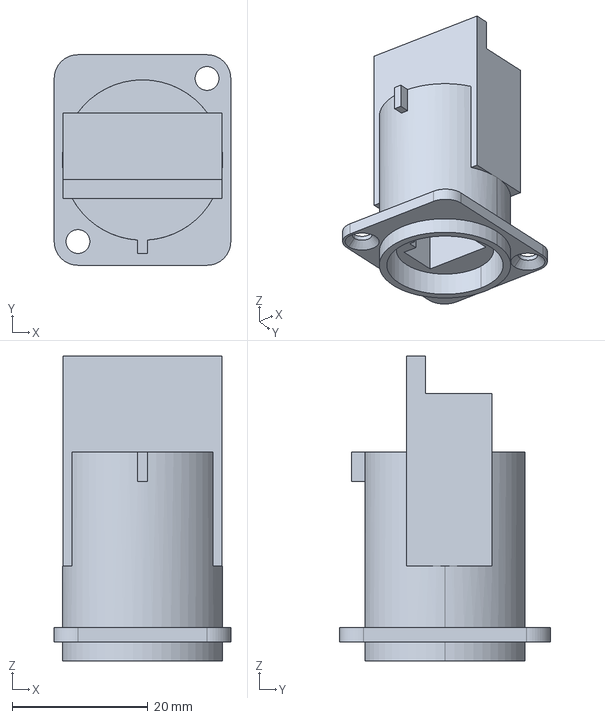
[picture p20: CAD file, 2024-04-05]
CAD/01. 3D_Drawings/03. Other_Components/panel_components/media_connectors/3-D NE8FDY-C6.stp
26.0 x 31.0 x 44.9 mm

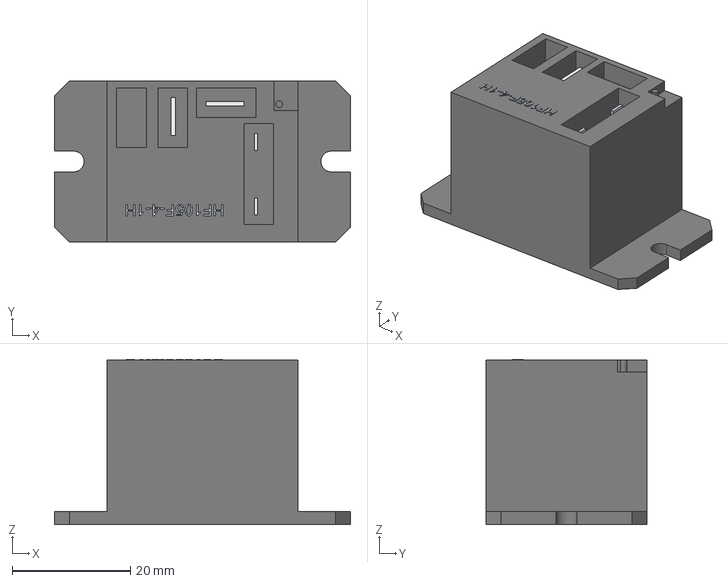
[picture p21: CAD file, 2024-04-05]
CAD/01. 3D_Drawings/03. Other_Components/power_distribution_components/HF105F-4/HF105F-4-1H.stp
50.0 x 27.2 x 27.9 mm

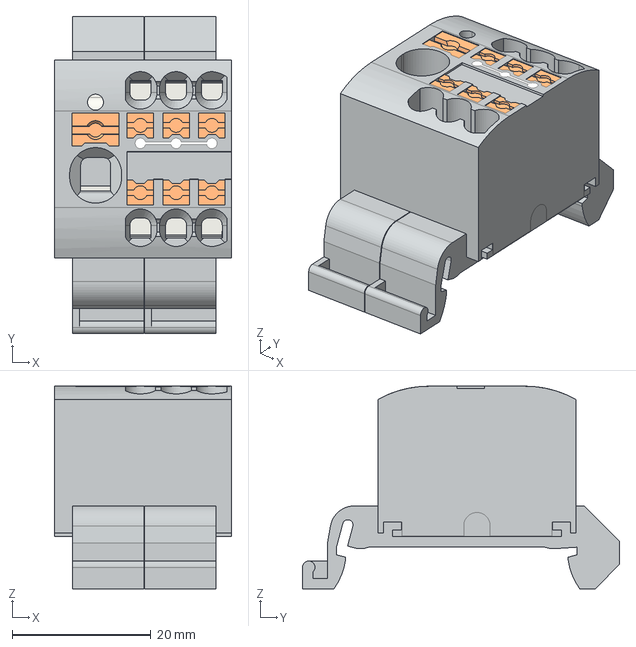
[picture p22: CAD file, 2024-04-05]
CAD/01. 3D_Drawings/03. Other_Components/power_distribution_components/ptfix/ptfix_6.stp
25.5 x 45.7 x 29.2 mm

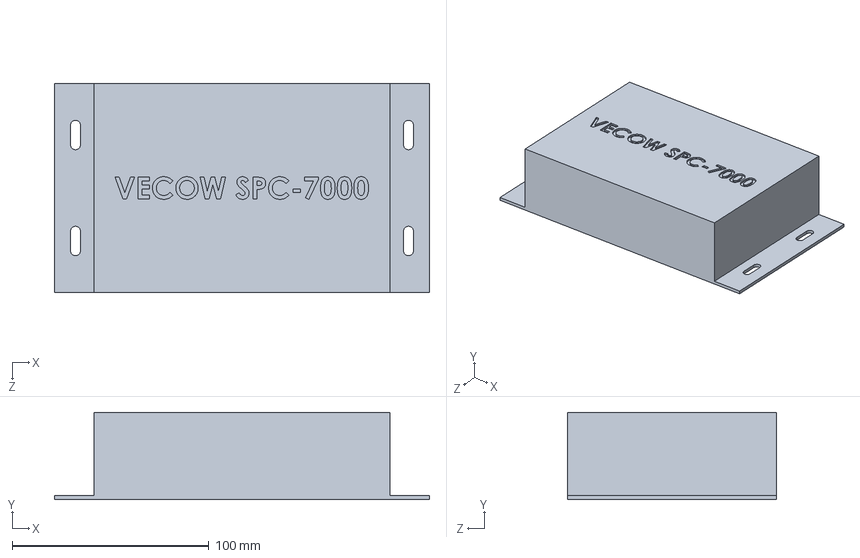
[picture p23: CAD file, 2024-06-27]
CAD/01. 3D_Drawings/03. Other_Components/Vecow spc-7000.SLDPRT
190.4 x 44.2 x 106.2 mm

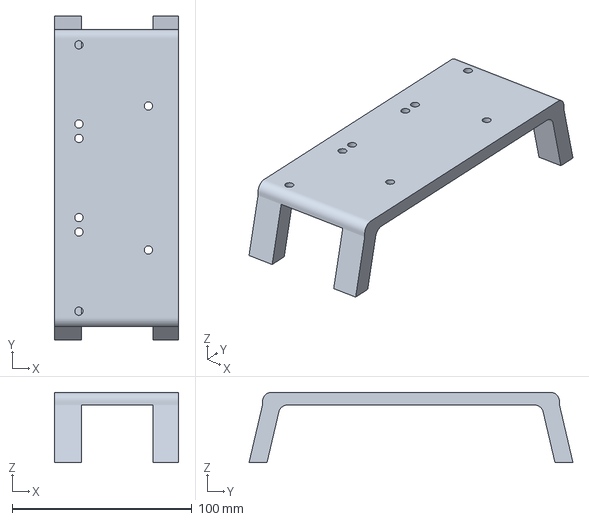
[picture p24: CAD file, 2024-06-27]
CAD/02. Production_Drawings/01. 3D_Print_Components/PWR DISTR Mount4.6.3MF
69.0 x 180.0 x 39.1 mm

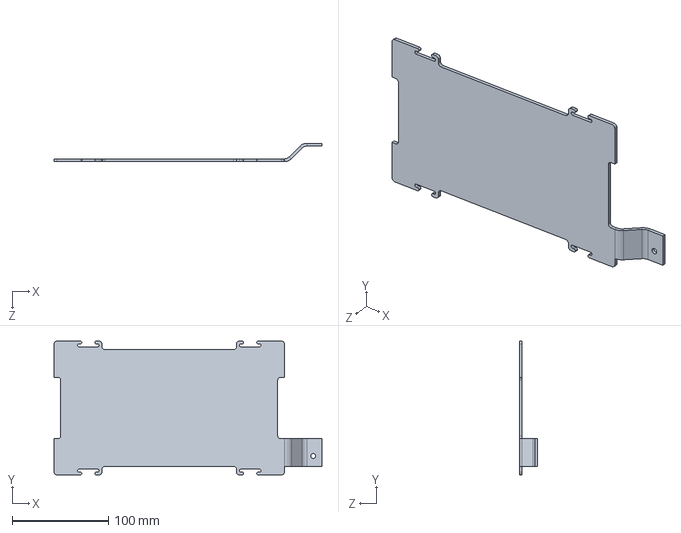
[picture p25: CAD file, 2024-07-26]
CAD/01. 3D_Drawings/02. Sheet_Metal_Components/LaserHunterMount.SLDPRT
279.1 x 139.4 x 19.2 mm

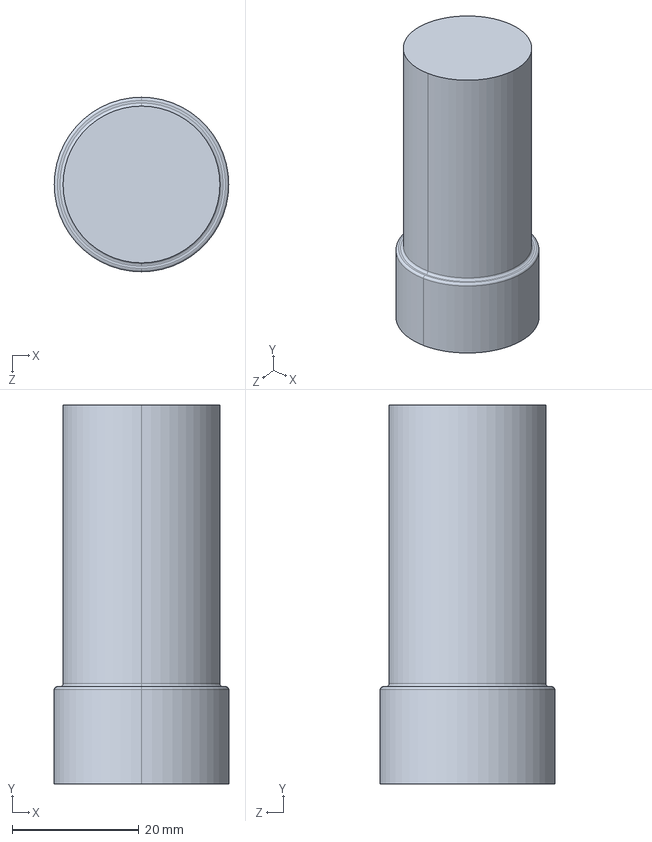
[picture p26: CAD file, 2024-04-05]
CAD/01. 3D_Drawings/03. Other_Components/H-RTK F9P HNSS/H-RTK F9P GNSS CH7604A.STEP
27.5 x 59.7 x 27.5 mm

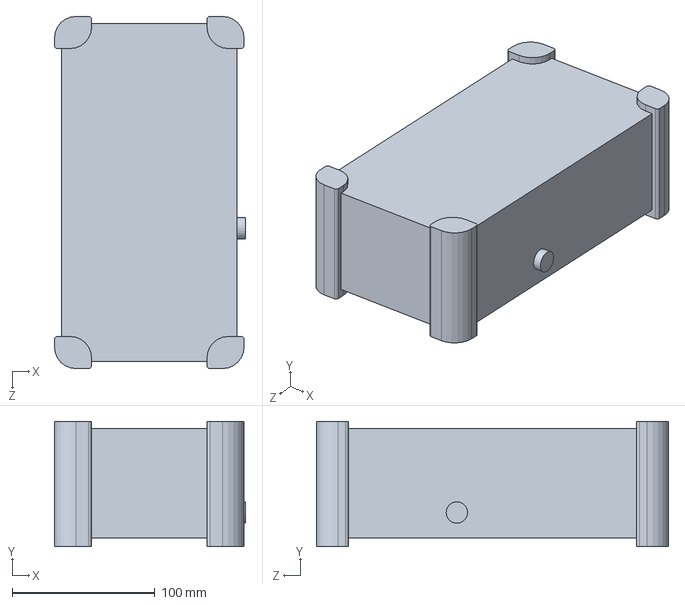
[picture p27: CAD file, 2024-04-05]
CAD/01. 3D_Drawings/03. Other_Components/LaserHunter.SLDPRT
134.0 x 88.0 x 247.0 mm

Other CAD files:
CAD/02. Production_Drawings/02. Sheet_Metal_Components/Panel Front.STEP
CAD/01. 3D_Drawings/01. 3D_Print_Components/PWR DISTR Mount.SLDPRT
CAD/01. 3D_Drawings/03. Other_Components/panel_components/LED_Button16mm/Thread.SLDPRT
CAD/01. 3D_Drawings/03. Other_Components/panel_components/media_connectors/RJ45_socket_black.SLDPRT
CAD/01. 3D_Drawings/01. 3D_Print_Components/heat_insert_test_print.SLDPRT
CAD/01. 3D_Drawings/02. Sheet_Metal_Components/GPS mount enforcement v15.step
CAD/01. 3D_Drawings/02. Sheet_Metal_Components/GPS mount.SLDPRT
CAD/01. 3D_Drawings/02. Sheet_Metal_Components/Mounting Plate.SLDPRT
CAD/01. 3D_Drawings/02. Sheet_Metal_Components/Outer Shell.SLDPRT
CAD/01. 3D_Drawings/02. Sheet_Metal_Components/Panel Back.SLDPRT
CAD/01. 3D_Drawings/03. Other_Components/Cable Grommet/51540_01.SLDPRT
CAD/01. 3D_Drawings/03. Other_Components/Cable Grommet/51540_02.SLDPRT
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

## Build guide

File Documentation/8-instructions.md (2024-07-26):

## Instructions

This section gives following set of instructions:
* [Manufacturing Instructions](/Documentation/8.1-manufacturing-instructions.md)
* [Assembly Instructions](/Documentation/8.2-assembly-instructions.md)
* [Mounting Instructions](/Documentation/8.3-mounting-instructions.md)

In addition you can find in [this](/Documentation/8.4-list-of-screws.md) document a list that summarizes the specific screws needed for assembly and mounting. 

*Note: this section has been adjusted from chapter 10 "Deployment" of Simon Brown's guide for agile software architecture to "Instructions", as this fits better for this hardware project*.

***

> ➡️ [Next: Manufacturing Instructions](./8.1-manufacturing-instructions.md)

> ⬅️ [Previous: Implementation](./07-Implementation.md)

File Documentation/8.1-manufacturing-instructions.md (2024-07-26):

## Manufacturing Instructions

This sections includes manufacturing instructions for the sheet metal and 3D printed parts of the backpack.

### Sheet Metal Parts

`.SLDPRT` and `.step` files of the sheet metal parts can be found in `CAD/01. 3D_Drawings/02. Sheet_Metal_Components` and `CAD/02. Production_Drawings/02. Sheet_Metal_Components` respectively. All sheet metal parts are designed for 3mm aluminum sheet metal.

Within CHARISMA, we let these sheet metal parts be manufactured by [247TailorSteel](https://www.247tailorsteel.com/en) by uploading the `.step` files in [SOPHIA](https://www.247tailorsteel.com/en/sophia). In SOPHIA,  select 
- Material: 3mm AlMg3 EN AW 5754 H111
- Cutting: Oxygen

If you design your own parts make sure that they are compatible with SOPHIA. You can find design guidelines [here](https://www.247tailorsteel.com/en/service/submission-rules-and-guidelines). 
If you choose a different manufacturer make sure you are complying with their guidelines (e.g. for bending parts and screw hole sizes and locations). 

### 3D Printed Parts

`.SLDPRT` and `.3MF` files of the 3D printed parts can be found in`CAD/01. 3D_Drawings/01. 3D_Print_Components` and `CAD/02. Production_Drawings/01. 3D_Print_Components` respectively.. All 3D printed parts have been printed with:
- PLA
- 30% infill
- Default settings in [CURA](https://ultimaker.com/software/ultimaker-cura/) (5.6.0)

Furthermore, all 3D printed parts have been designed to be used with heat set inserts. 
Insert the heat set inserts with a soldering iron. Tip: don’t insert the last bit of the insert with the soldering iron, but quickly push it in with a flat surface (e.g. a table) in order to make it flush.

If you use different heat set inserts than specified in the parts list (see `Other Files`), you may need to adjust the hole diameter of these parts. You can use the `heat_insert_test_print.SLDPRT` file as a test file for finding the proper hole dimensions. You also find these [guidelines](https://www.spirol.com/assets/files/ins-wp-how-to-design-the-proper-hole-for-heat-ultrasonic-inserts-us.pdf) useful for adjusting the heat set insert holes.

### Vinyl Wrap (Optional)

You may want to apply vinyl wrap to the sheet metal to make it look more professional. 
You can roughly follow the steps described [here](https://www.wikihow.com/Apply-Vinyl-Wrap). Furthermore, to remove excess vinyl wrap, you can also use a small file. This is especially handy for smaller parts and screw holes. 

<p align="center" width="100%">
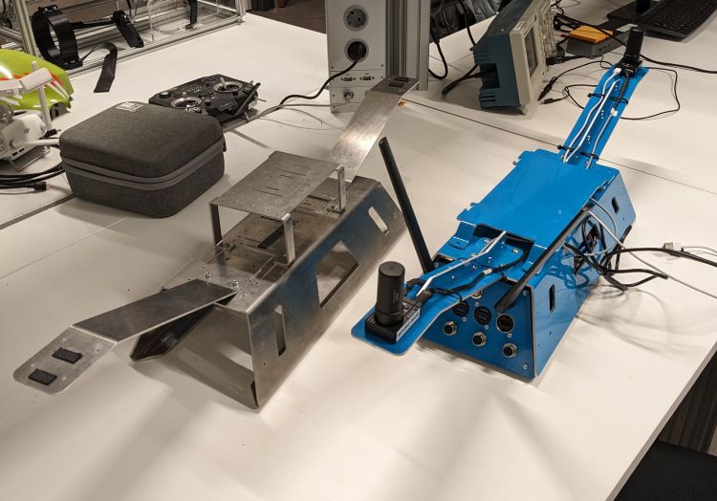
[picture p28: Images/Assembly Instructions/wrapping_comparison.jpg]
    
    <br>
    <em>Comparison of backpacks with and without vinyl wrapping.</em>
</p>

***

In the next section you can read on how to assemble the backpack.

> ➡️ [Next: Assembly Instructions](./8.2-assembly-instructions.md)

> ⬅️ [Previous: Instructions](./8-instructions.md)

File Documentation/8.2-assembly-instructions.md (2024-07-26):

## Assembly Instructions

This section describes how to assemble the backpack.

### Step 1: Sheet metal and 3D printed parts

Create the sheet metal and 3D printed parts as described in the [manufacturing section](/Documentation/8.1-manufacturing-instructions.md).  

### Step 2: Insert rivets nuts 

Next, insert rivet nuts into the top holes of the outer shell and the side bends of the mounting plate as shown in figure 1. You may need to hammer  the rivets into the holes, due to the low tolerance. 

> ⚠️**Note:** Be careful with the side bends, it may be better to just file away a little of the aluminum than hammering in the rivets, as too much force may deform the bends.

Once you have inserted the rivets nuts into the holes, you will need to permanently insert them using a rivet tool. 

> ⚠️**Note:** Be careful that you do not apply too much force as you may damage the threading of the rivets nuts.

<p align="center">
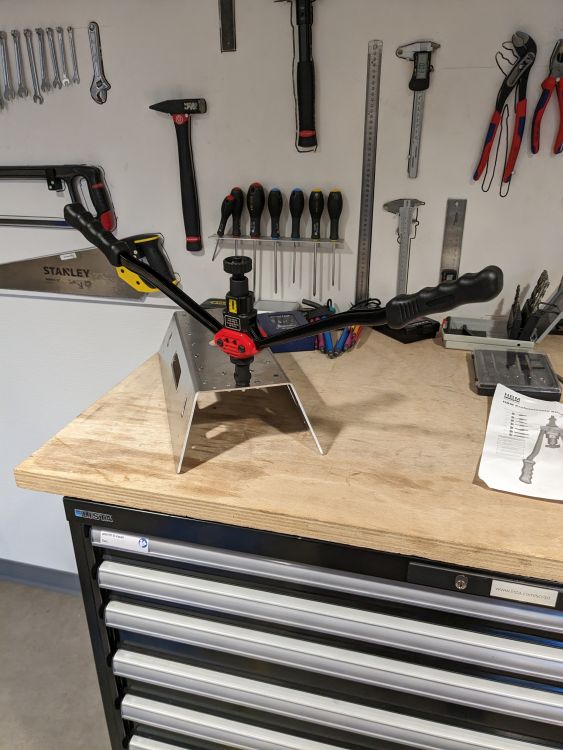
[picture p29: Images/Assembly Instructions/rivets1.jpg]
    
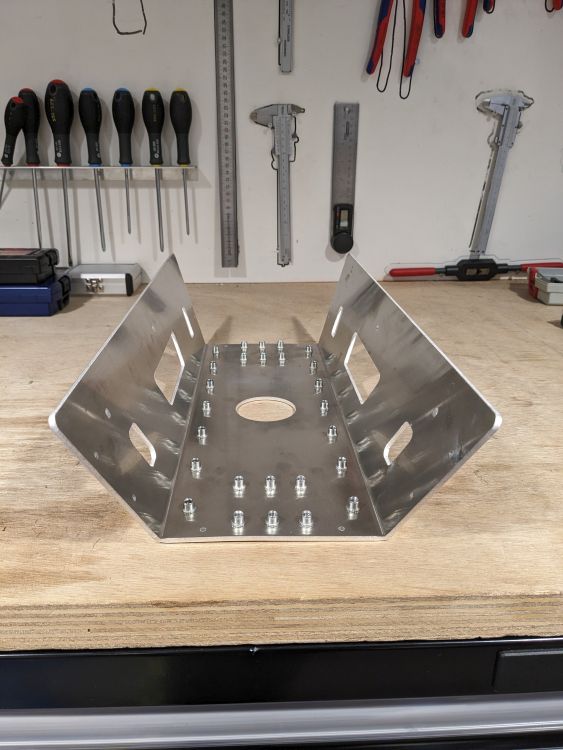
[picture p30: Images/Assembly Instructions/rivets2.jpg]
    
    <p align="center"><i>Figure 1: Installing rivet nuts with a rivet tool.</i></p>
</p>

### Step 3: Assemble the panels
Next, assemble as the panels as shown in figure 2. For each panel you will need 4x M3x10 screws to screw the panel onto the 3D printed bracket. For the interface panel, it's advised to start from the bottom up: First insert the M12 power connectors, then the media connectors (from left to right: Ethernet, 2x USB, HDMI) and then finally the power button and the female RP-SMA connectors for the WIFI antennas. For the media connectors, use 8x M3x12 screws.

<p align="center" width="100%">
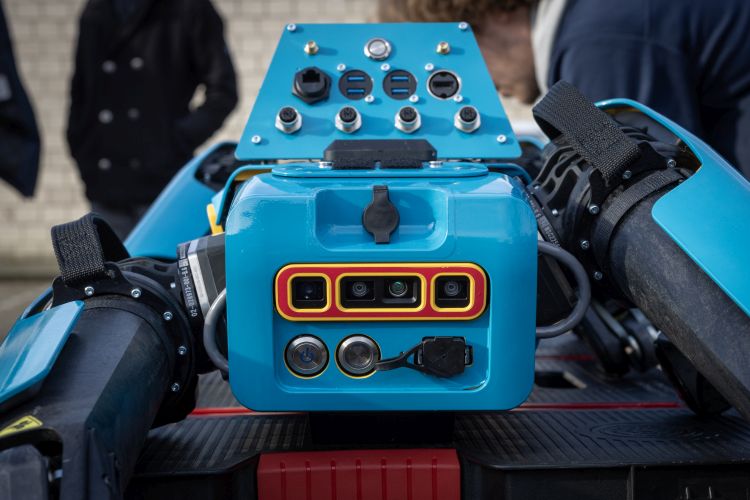
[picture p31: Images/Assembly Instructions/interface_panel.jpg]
    
    <br>
    <em>Figure 2: Interface panel.</em>
</p>

***

### Step 4: Assemble power distribution
Next, assemble the power distribution. You can find a circuit diagram shown in figure 3:

<p align="center" width="100%">
    
    <br>
    <em>Figure 3: Electrical diagram of the power distribution.</em>
</p>

After you have printed the power distribution mount, you have to insert the heat set inserts using a soldering iron. 
Next, you will need a DIN rail of approximately 15 cm length. Screw the DIN rail into the heat inserts on top of the mount using 2x M3x8 screws with washers. The result should look like figure 4.
Next, slide the PTFIX connectors onto the DIN rail and screw in the relays blocks.

<p align="center">
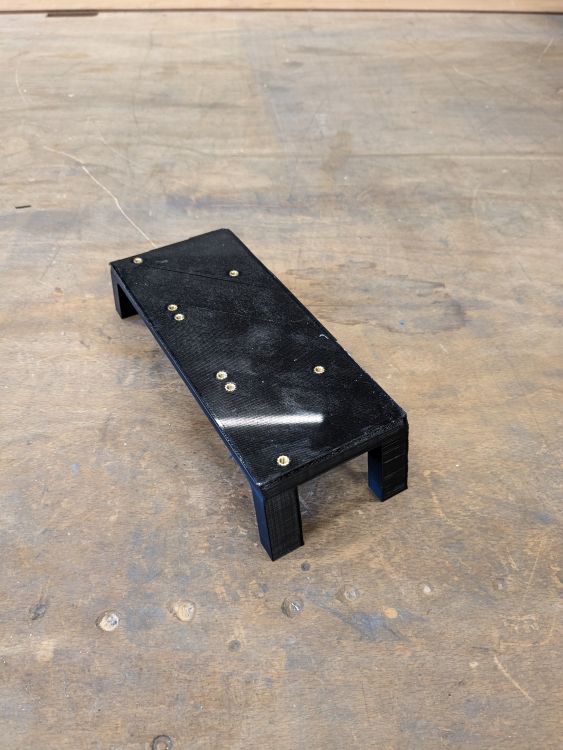
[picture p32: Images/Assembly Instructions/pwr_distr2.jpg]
    
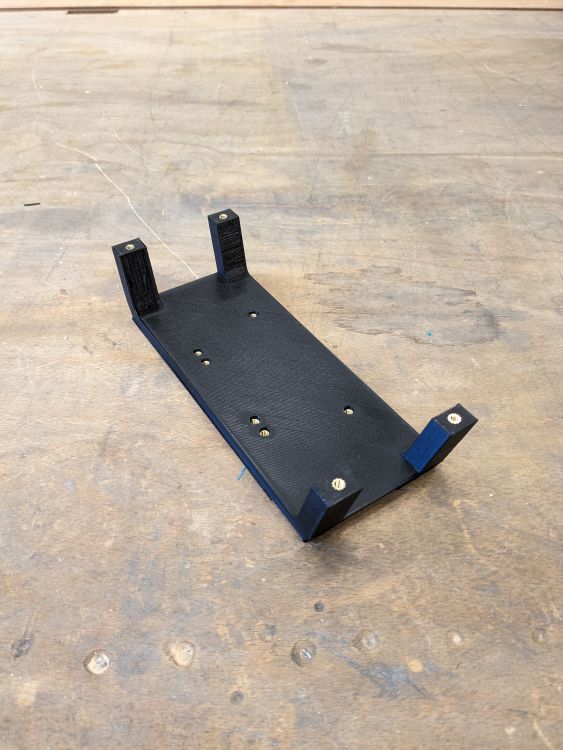
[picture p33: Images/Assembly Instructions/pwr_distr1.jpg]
    
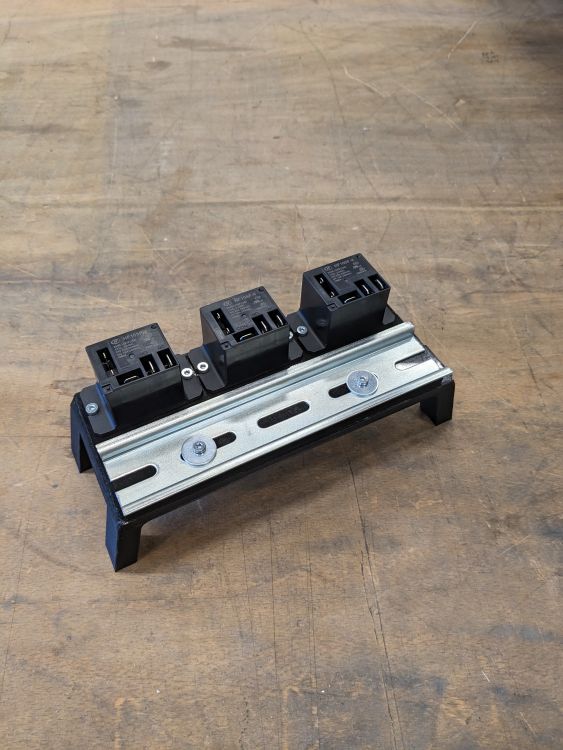
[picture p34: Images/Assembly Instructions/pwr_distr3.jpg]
    
    <p align="center"><i>Figure 4: Power Distribution mount (without PTFIX blocks).</i></p>
</p>

**VGA connector**

Next, you will need to solder a VGA / HD15 connector for the GXP, you can find the pinout of the GXP [here](https://support.bostondynamics.com/s/article/Spot-General-Expansion-Payload-GXP).
For this custom connector you will need the following pins:

* GND: 1-4
* 5V: 15
* 12V: 7-8
* 24V: 13-14

Before soldering the wires to it, make sure they are at least 50 cm long.
Once you are done soldering, you can add a braided sleeve around the wires to organize them neatly as shown in figure 5.

<p align="center">
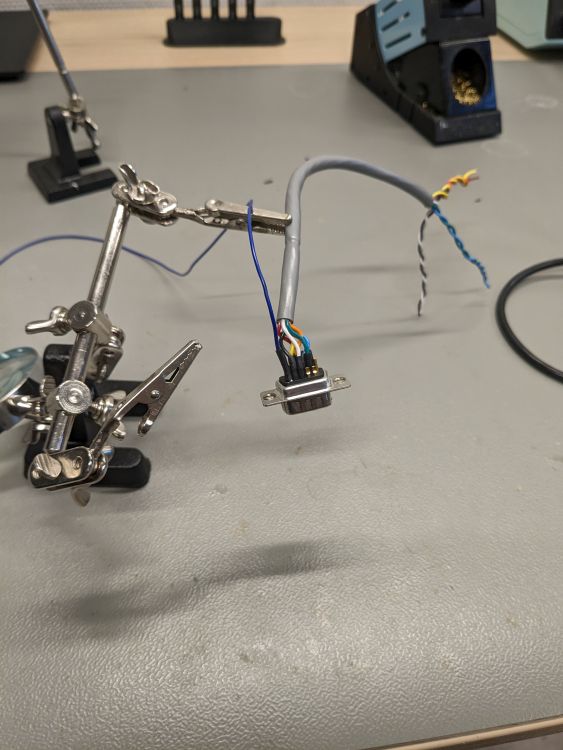
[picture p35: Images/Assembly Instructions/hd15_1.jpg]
    
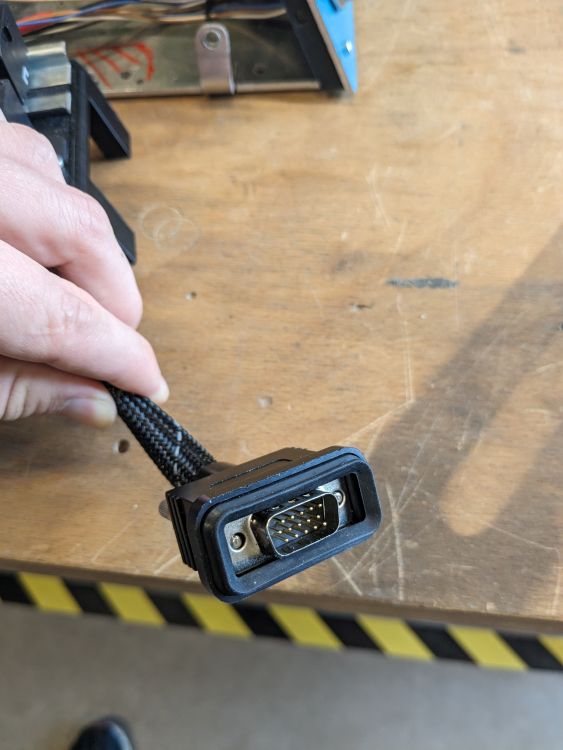
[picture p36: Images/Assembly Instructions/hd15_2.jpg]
    
    <p align="center"><i>Figure 5: Soldering custom HD15 connector for the GXP.</i></p>
</p>

***

**Mount panel, GXP and  power distribution block**

Next, mount the interface panel (the one with all the connectors), the GXP and the power distribution mount. 

Start with mounting the 3D printed bracket for interface panel by inserting 2x M3x10 screws from the bottom of the main mounting plate as shown in figure 6. 

> ⚠️**Note:** The left and right side of the mounting plate differ in length. Make sure to connect this panel to the longer side, as shown below.

<p align="center">
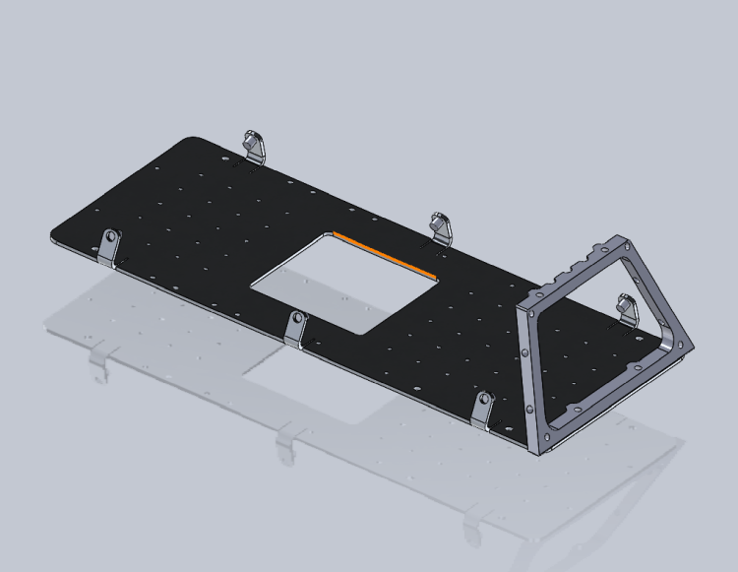
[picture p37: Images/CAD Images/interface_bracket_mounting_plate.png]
    
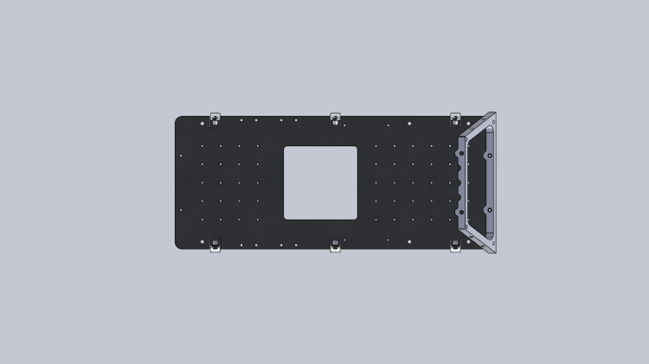
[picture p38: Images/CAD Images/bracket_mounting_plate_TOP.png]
    
    <p align="center"><i>Figure 6: SolidWorks assembly of mounting plate and 3D printed interface bracket. Note how the right side of the mounting plate is longer than the other.</i></p>
</p>

Next, place the GXP onto the plate and mark its outline on the mounting plate as shown in figure 7. Afterwards, you can route the wires coming from the interface panel through the holes beneath the GXP. It's best to zip tie the wires to the mounting board.

<p align="center">
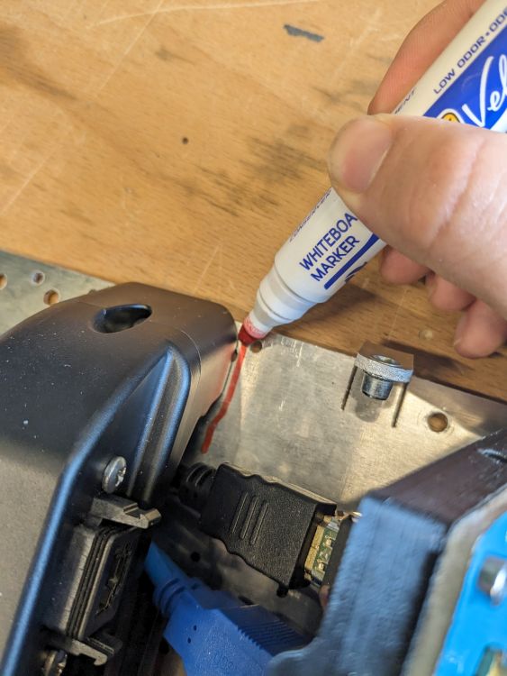
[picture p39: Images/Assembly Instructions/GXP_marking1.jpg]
    
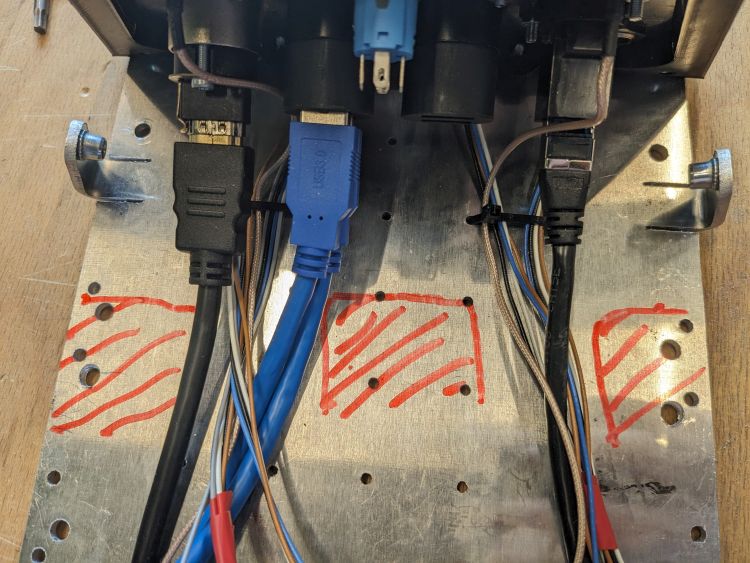
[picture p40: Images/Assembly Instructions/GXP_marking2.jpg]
    
    <p align="center"><i>Figure 7: Marking outline of the GXP in order to route the wires from the interface panel beneath the GXP.</i></p>
</p>

Next, mount the GXP to the main mounting plate using 2x M5x20 screws as shown in figure 8 (left), use nuts at the bottom of the mounting plate. Make sure the ethernet and HD15 port face towards the interface panel. 
Take the cable from the GXP and lay it out to the left as shown below. Finally, you can mount the power distribution board with the relays facing the GXP. Here, use 4x M3x8 screws.

<p align="center">
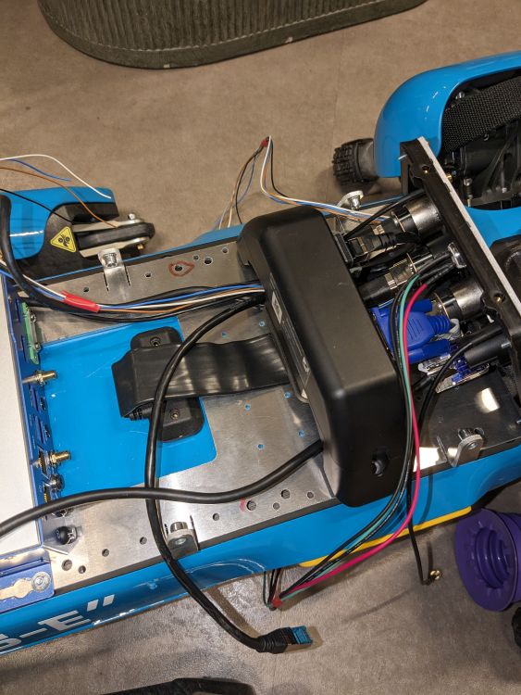
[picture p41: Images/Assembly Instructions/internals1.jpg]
    
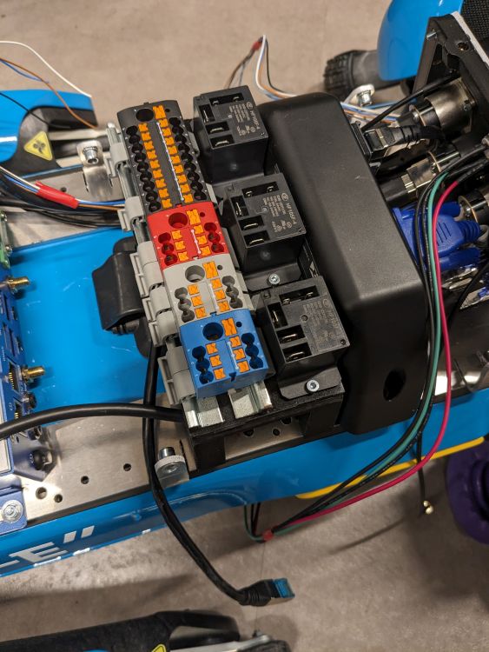
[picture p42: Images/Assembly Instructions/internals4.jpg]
    
    <p align="center"><i>Figure 8: Mounting the GXP (left) and then the power distribution mount (right).</i></p>
</p>

***

**Relays**

Next, we will connect the wires coming from the GXP to the the relays and the PTFIX connectors.

First we will take care of the power lines of the relays, which operate at 24V. Therefore, take both the 24V wires coming from the GXP and crimp them together with the N.O. connection of the power button (use a female spade connector) as shown in figure 9.

<p align="center" width="100%">
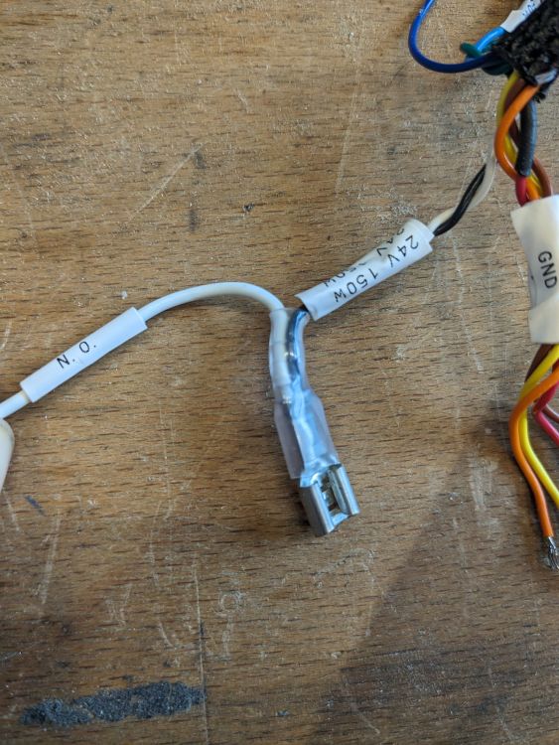
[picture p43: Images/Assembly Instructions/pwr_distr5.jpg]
    
    <br>
    <em>Figure 9: Crimped wires of the 24V line of the GXP with the N.O. port of the power button.</em>
</p>

Insert this connector into the COM slot of the most of the right relay. Next, crimp the wire from the COM port of the power button and another red wire of approximately 6 cm length and connect it to the positive power connection of the same relay as shown in figure 10 (left).
Then, we will continue the positive power line of the relays. Crimp together the loose red wire with another red wire and insert it into the middle relay. Finally, crimp the end of the just added wire together and insert it in into the last relay. 
Afterwards, crimp together 3 black wires such that you can connect the ends to all 3 ports of the negative power line for the relays as well as to the ground PTFIX block.

<p align="center">
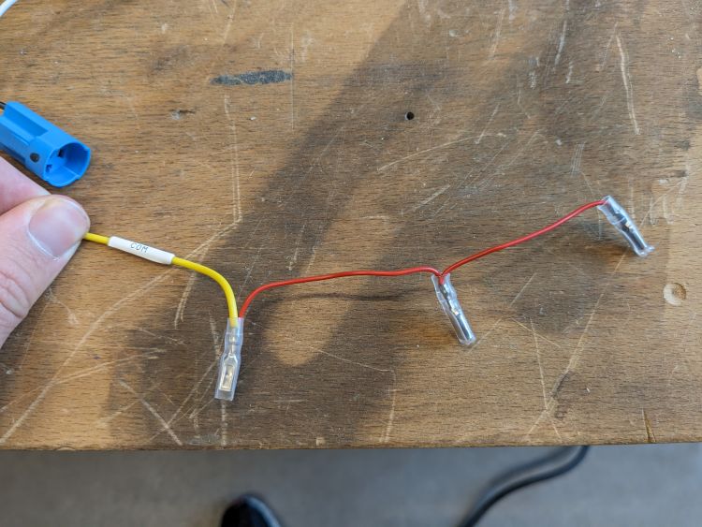
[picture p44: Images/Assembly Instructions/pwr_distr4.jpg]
    
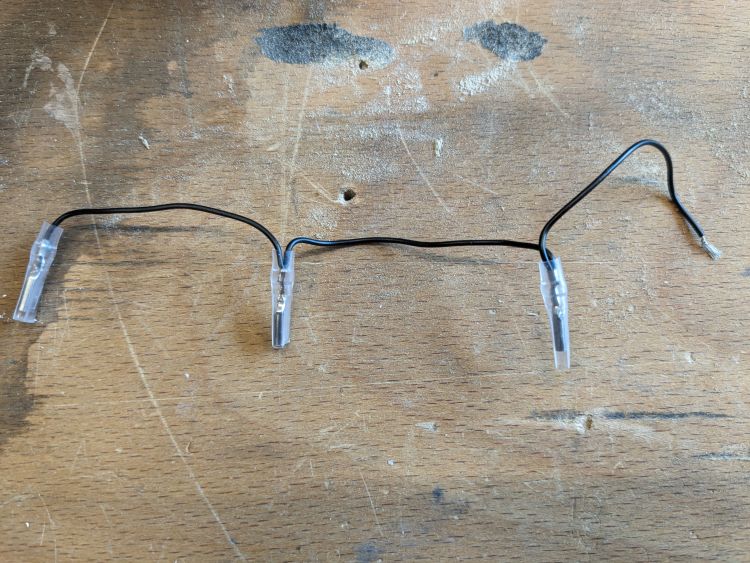
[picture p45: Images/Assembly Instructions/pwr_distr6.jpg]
    
    <p align="center"><i>Figure 10: Crimped wires of the positive (left) and negative power lines (right) of the relays.</i></p>
</p>

Next, take the 2 12V leads coming from the GXP, crimp them together and insert them into the COM port of the middle relay. Afterwards, take the 5V lead from the GXP and crimp it together with a female spade connector and insert it into the COM port of the last relay.

You can test at this point if the relay system works: connect the GXP to SPOT, power on SPOT and press the power button of the panel. You should read now 24V, 12V and 5V respectively at the N.O. ports of the relays; the LED of the power button will not light up just yet as we did not connect it to the 5V line yet.

***

**Fuses to PTFIX**

Next, we will connect the relays to the PTFIX blocks. 
For the both the 24V and 12V, we insert an inline fuse in between, where we add a 5A and a 10A fuse blade into the fuse holders respectively. This is because the GXP shares the 12V and the 24V line (150W) and we want to reserve 40W for the PC. Crimp a female spade connector to each of the inline fuses, insert them into the N.O. port of the relay, and insert the other end into the large hole of PTFIX connector.

Finally, take another inline fuse holder and crimp it together with a red wire. Insert the crimp into the N.O. connector of the relay, insert other end of the fuse holder into the large hole of the PTFIX connector. As the GXP returns the 5V at 10W, we will add a 2A fuse blade into the fuse holder. 
Next, solder a 82 Ohm resistor to the red wire, slide a heat shrink around it and solder the end of the resistor to the positive voltage connection of the LED of the power button (don't forget to add some heat shrink). The result should look like figure 11.

<p align="center" width="100%">
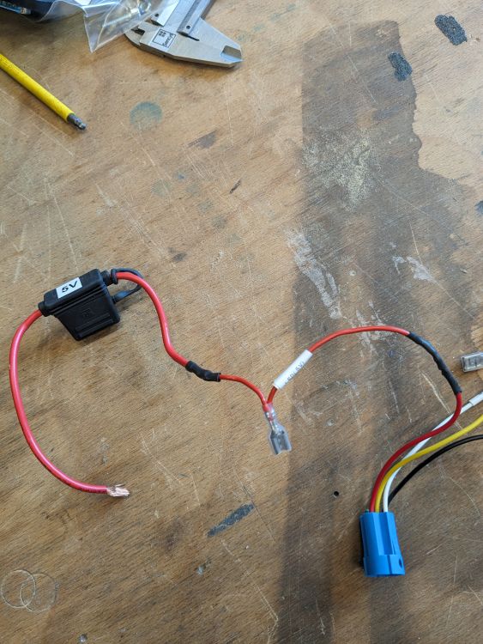
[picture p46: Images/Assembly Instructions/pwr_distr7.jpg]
    
    <br>
    <em>Figure 11: Crimped wires of the inline fuse and positive line of the power button (with 82 ohm resistor in between).</em>
</p>

If you now turn on SPOT and press the power button, the power button should light up and the PTFIX blocks should read out 24V, 12V and 5V respectively.

***

**M12 connectors**

Next, we will connect the M12 connectors to the PTFIX blocks as shown in the electrical diagram (see above). 
Here, we place for the 24V and the 12V lines inline fuses with a 4A fuse blades in between the PTFIX block and the M12 connectors, as the M12 connectors are rated for 4A. As the 5V line does provide power at 10W, it will never exceed the 4A rating of the M12 connectors, thus we do not need to add a fuse in between. 

Due to the limited space in the backpack, the inline fuse holders will be connected to 2 power lines, thus there will be 3 inline fuse holders: one that is shared between the 12V lines and two that will share two 24V lines each.
Cut the wires from the M12 connectors to appropriate length, and solder the positive leads together with the inline fuse holder. Connect the inline fuse holder to the respective PTFIX blocks, connect the ground leads from the M12 connector to the 18x6 PTFIX block.

If turn on SPOT and the power distribution of the backpack, you should be able to read out the respective voltages at the M12 connectors.

***

**PC**

Finally, we can connect the PC (here: VECOW SPC-7000) to the power distribution. 
Before we mount the PC, you have to connect ground and either 12V or 24V to the screw terminals of the PC. For robustness, you can apply some soldering iron to the leads that will be connected to the screw terminals. Make sure to also ground the PC to the mounting plate (if applicable), as shown in figure 12.

> ⚠️**Note:** If you choose to have a different PC, it may need a different voltage.

<p align="center" width="100%">
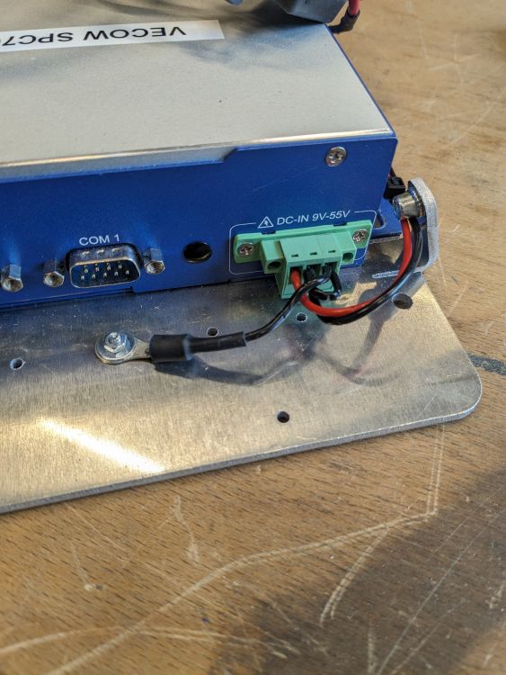
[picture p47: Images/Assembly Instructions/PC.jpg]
    
    <br>
    <em>Figure 12: Grounded PC.</em>
</p>

Afterwards, connect the HDMI, USB, ethernet and antenna cables and mount the PC to the mounting plate using 2x M3x8 screws with washers. Finally, you can connect the second panel to this side of the backpack.

### Step 5: GNSS Wings (Optional)

Next, you can add the GNSS "wings" to the outer shell of the backpack as shown in figure 13.

<p align="center" width="100%">
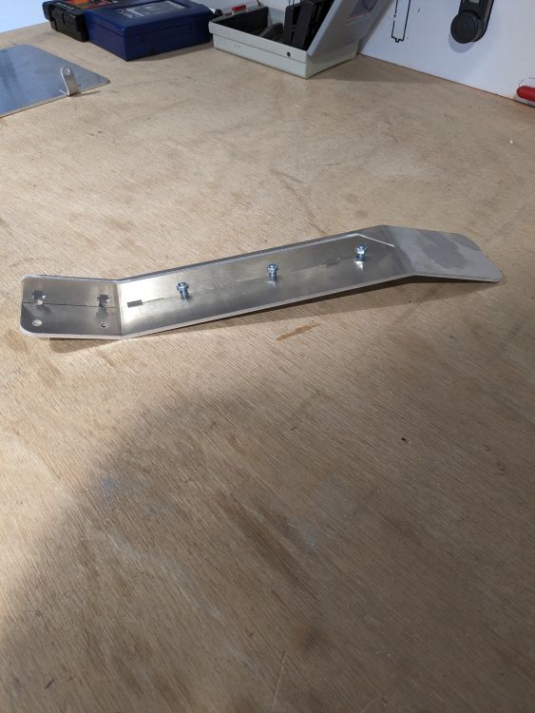
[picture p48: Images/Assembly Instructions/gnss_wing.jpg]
    
    <br>
    <em>Figure 13: GNSS wing with inserted brace for stability (without vinyl wrap).</em>
</p>

Start by inserting the braces into the wings using 5x M5x12 screws and nuts (first only the middle ones) per wing. Then mount the wings using 4x M5x16 screws to the outer shell. Afterwards, insert the last 2 screws to secure the brace from the bottom of the outer shell (2x M5x20). 

Finally, screw on the GNSS sensors onto the wings using 3x M2.5x8 screws. You can apply some foam to the mounting surface of the GNSS sensor as shown in figure 14. 

<p align="center" width="100%">
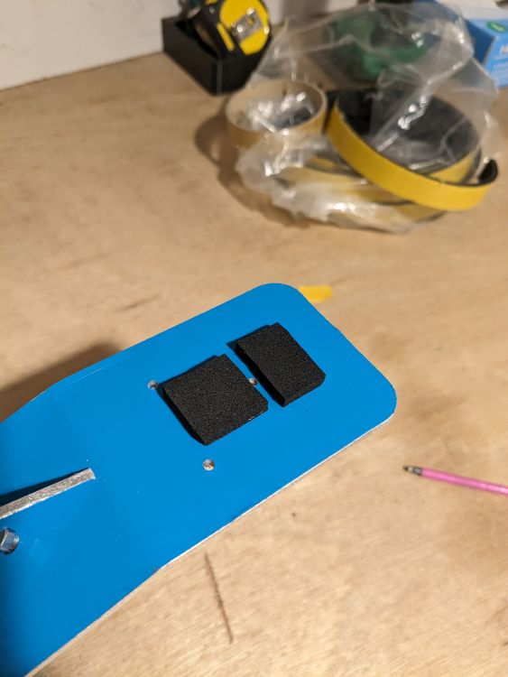
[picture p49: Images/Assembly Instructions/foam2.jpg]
    
    <br>
    <em>Figure 14: GNSS wing with foam for the GNSS sensors.</em>
</p>

Afterwards, add the GNSS sensors with the connection ports pointing towards the backpack, as shown in figure 15:

<p align="center" width="100%">
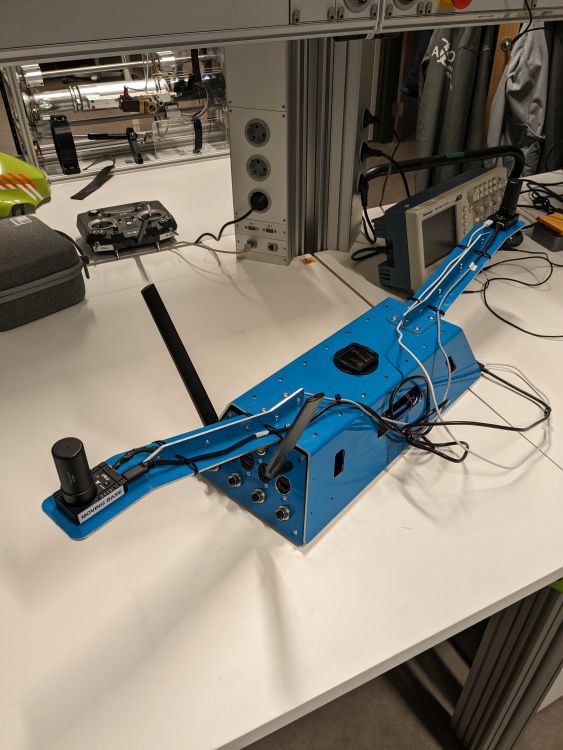
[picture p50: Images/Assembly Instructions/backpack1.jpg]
    
    <br>
    <em>Figure 15: Mounted GNSS sensors.</em>
</p>

Here, the wires are connected as shown in figure 16:

<p align="center" width="100%">
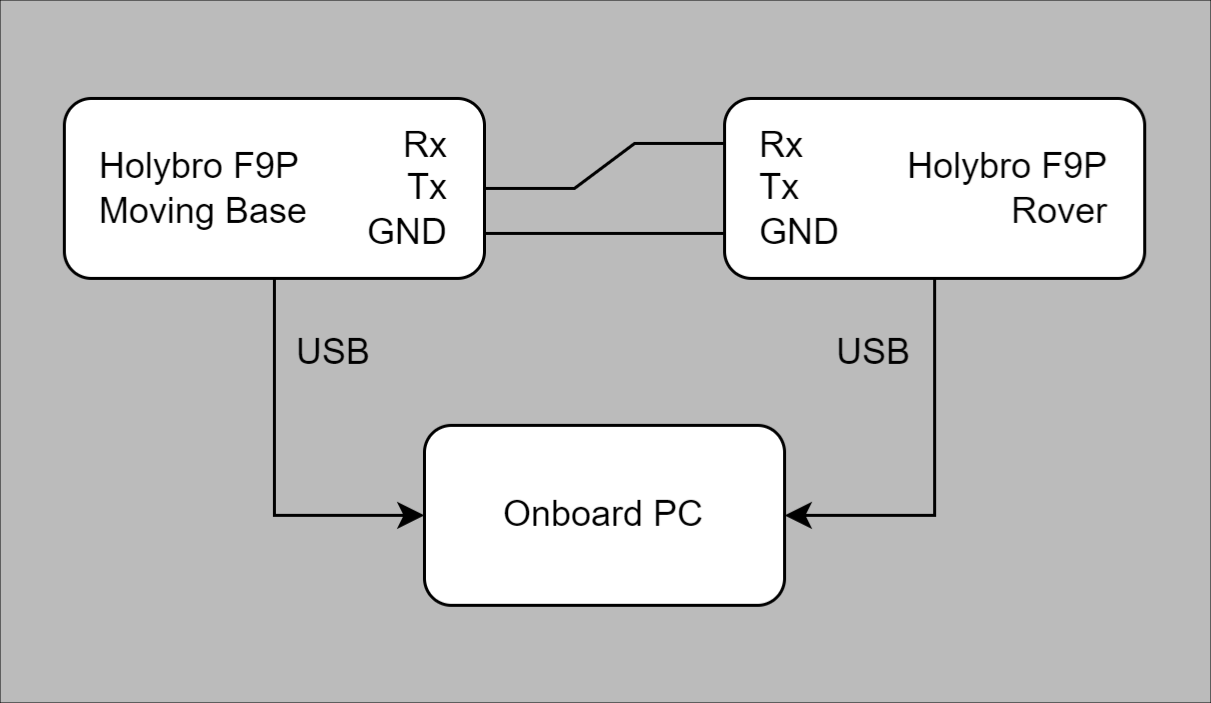
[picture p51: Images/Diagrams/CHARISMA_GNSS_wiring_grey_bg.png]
    
    <br>
    <em>Figure 16: Wiring of GNSS sensors.</em>
</p>

You may choose to connect the USB wires to the PC via the cable grommet or via the USB connectors on the interface panel.

***

In the next section you can read on how to mount the backpack onto SPOT.

> ➡️ [Next: Mounting Instructions](./8.3-mounting-instructions.md)

> ⬅️ [Previous: Manufacturing Instructions](./8.1-manufacturing-instructions.md)

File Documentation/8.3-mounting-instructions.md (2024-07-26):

## Mounting Instruction

In this section we will describe how to mounted the assembled backpack onto SPOT. 

### Step 0: Preparation
Make sure SPOT is lying down on a even and stable surface. For example the ground or on top of a workbench. If you want to use the GPS antennas, they should be already mounted on the backpack.

### Step 1: Mounting rails

**Required tools:**
* Philips screw driver PH1

First, remove the middle payload cap of SPOT as indicated in Figure 1. 

> ⚠️**Note:** Make sure to save the cap of SPOT somewhere secure as the robot will [not work](https://dev.bostondynamics.com/docs/payload/robot_electrical_interface) if either the GXP or the payload cap is not connected!

<p align="center" width="100%">
    
    <br>
    <em>Figure 1: Middle payload cap on SPOT.</em>
</p>

Next, place M5 sliding T-nuts into the mounting rails of spot, as depicted in Figure 2. Make sure that these are locking nuts, so they will stay in place. You can start by placing (and locking) two sliding nuts at the edge of the rail in the back. Then place the other two sliding nuts at a distance of 36 cm (hole to hole) and lock them. Verify whether the holes of the backpack line up with the holes of the sliding nuts and mark their locations (e.g. using masking tape).

<p align="center">
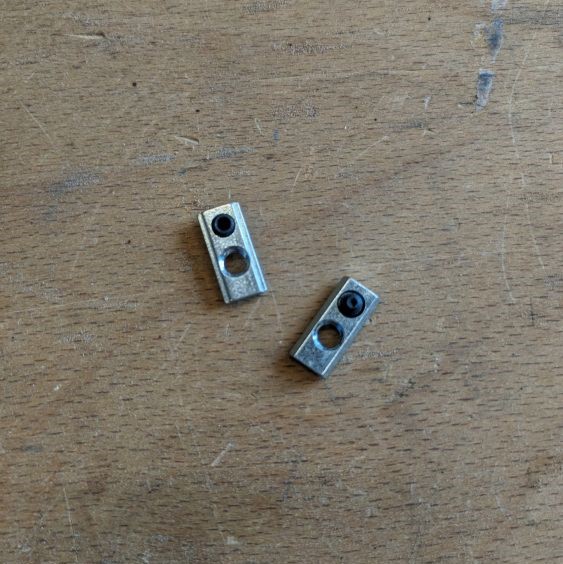
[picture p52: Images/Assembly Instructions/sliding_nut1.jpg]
    
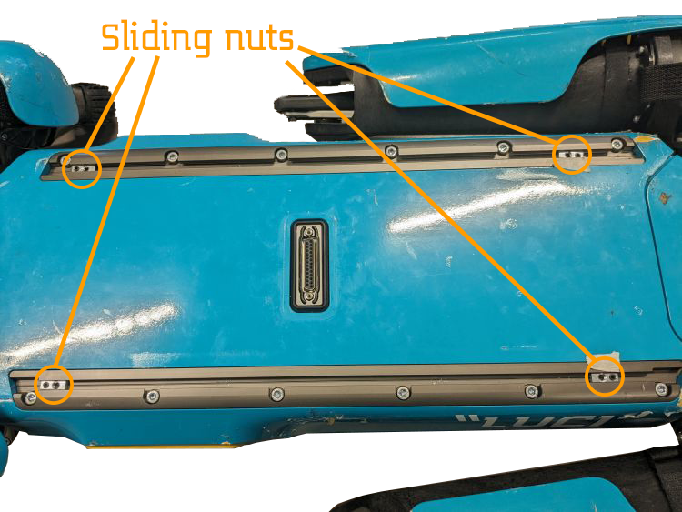
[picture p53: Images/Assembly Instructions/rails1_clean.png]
    
    <p align="center"><i>Figure 2: Sliding nuts inserted into the mounting rails of SPOT.</i></p>
</p>

### Step 2: Remove the backpack cover 

**Required tools:**
* Allen key nr 2.5 (top screws)
* Allen key nr 3 (side screws)

*Assuming that the base plate and the cover of backpack have been previously screwed together:*

Remove the eight screws holding the top cover of the backpack, four on the top and two on each side (indicated in the Figure 3 below). *Store them temporarily in a safe place*, we need them again to secure the top cover. Gently lift the top cover of the backpack and place it aside.

> ⚠️**Note:** If the GSP antennas are connected to the backpack, the USB cables may be still connected and running through the top cover. Please handle them with care. You may disconnect the cables from the PC if this makes the process easier.

<p align="center">
    
    
    <p align="center"><i>Figure 3: Removing side and top screws of the backpack cover.</i></p>
</p>

### Step 3: Connect the GXP

**Required tools:**
* Philips screwdriver PH1

Before we actually mount the backpack to the rails, it's best to connect the GXP first to SPOT. Place the mounting plate onto SPOT and make sure the interface panel is facing to the back. Then, slightly lift up the plate and insert the BD50 cable of the GXP to SPOT (You may need to loosen the screws of the connector first). Make sure the existing cable is facing towards the front of SPOT as depicted in Figure 4.

<p align="center" width="100%">
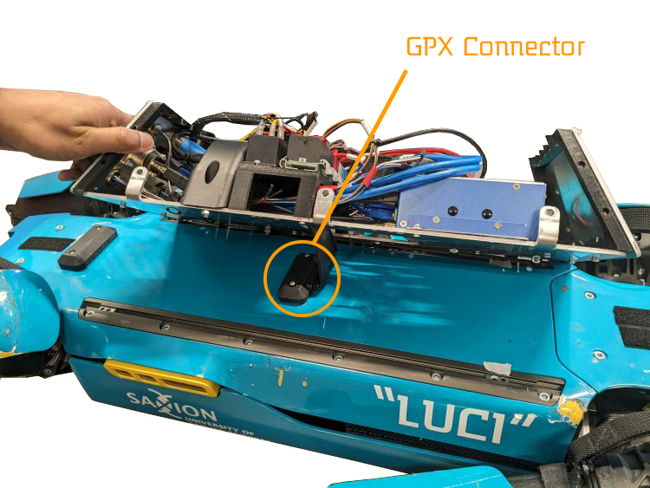
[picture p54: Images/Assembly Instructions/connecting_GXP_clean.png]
    
    <br>
    <em>Figure 4: Lifting the mounting plate up in order to connect the GXP.</em>
</p>

Gently lower the backpack onto the mounting rails of spot. Take a Philips screwdriver PH1 and tighten (not too tight!) the GXP connector from above, see Figure 5. 

<p align="center" width="100%">
    
    <br>
    <em>Figure 5: Lifting the mounting plate up in order to connect the GXP.</em>
</p>

 > ⚠️**Note:** Then, screw on the GXP connector, SPOT might not work otherwise!

### Step 4: Securing the mounting plate on SPOT

**Required tools:**
* Allen key nr 3

In order to secure the backpack screw-in the four M5x12 screws through the mounting holes into the sliding nuts. Figure 6 indicates the mounting holes of the backpack.

<p align="center" width="100%">
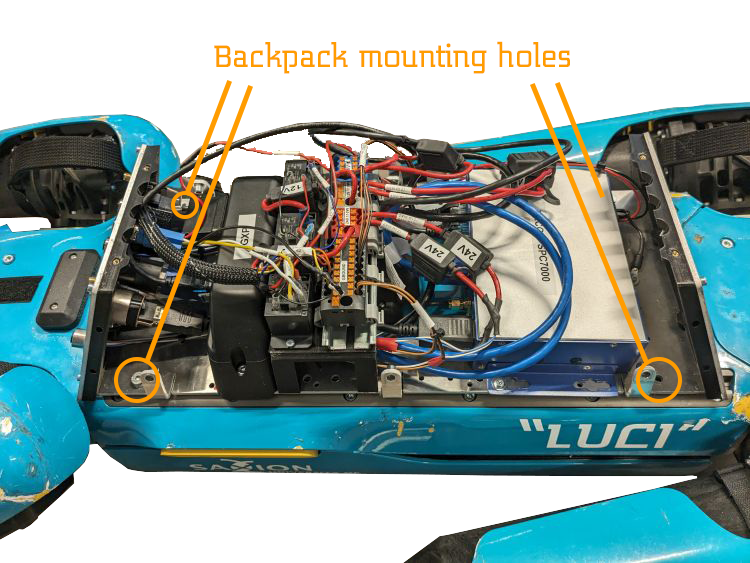
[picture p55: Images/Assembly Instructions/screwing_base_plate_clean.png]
    
    <br>
    <em>Figure 6: Mounting holes to secure the backpack onto SPOT.</em>
</p>

### Step 5: Connect the outer shell to the mounting plate

**Required tools:**
* Allen key nr 2.5
* Allen key nr 3

Now the cover of the backpack can be placed, make sure no cables are in the way or get damaged. 

Next, place outer shell on of the backpack top and screw the panels on from the top using 4x M3x10 screws (you can omit the sides of the panels). Next screw the sides of the outer shell to the bends of the main plate using 4x M5x16 screws (You can omit the holes in the middle of the shell).

This is the reverse operation of Step 2.

Voila! The result should look like the one in figure 7 (minus the payload).
<p align="center" width="100%">
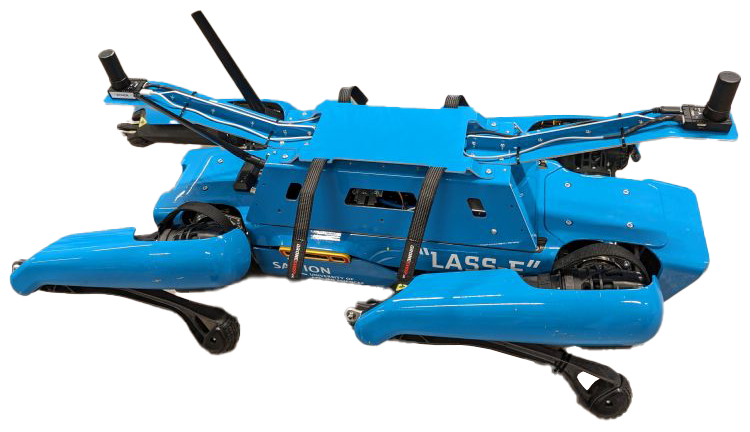
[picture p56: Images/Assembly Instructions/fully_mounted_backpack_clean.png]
    
    <br>
    <em>Figure 7: Fully mounted backpack on SPOT (with Laser Hunter mount and GNSS sensor mounts).</em>
</p>

### Step 6: Attach any other payload.
Attach any other additional payload to the outer shell (e.g. see the Laser Hunter mount on the top). If you need to use the cable grommet, you will first need to dismount the outer shell in order to connect any cables to the PC and the power distribution.

***

In the next section you can check what and how many screws are being used for specific parts of the backpack.

> ➡️ [Next: List of screws](./8.4-list-of-screws.md)

> ⬅️ [Previous: Assembly Instructions](./8.2-assembly-instructions.md)

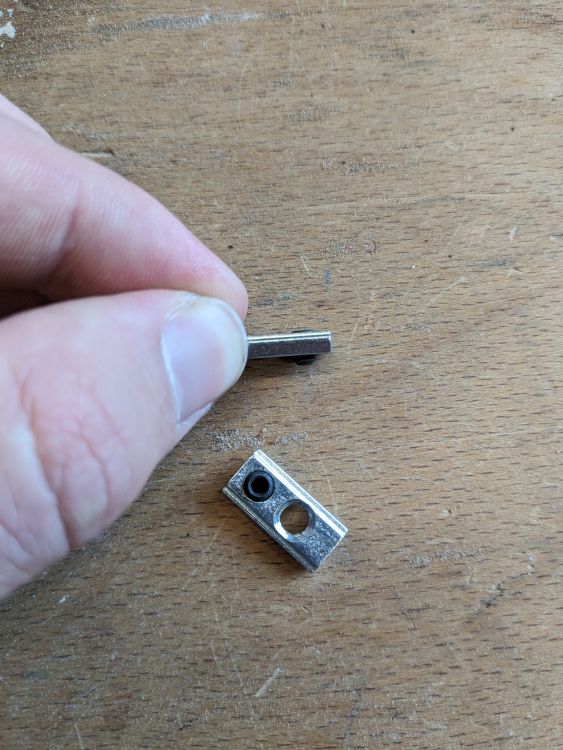
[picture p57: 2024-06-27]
Images/Assembly Instructions/sliding_nut2.jpg

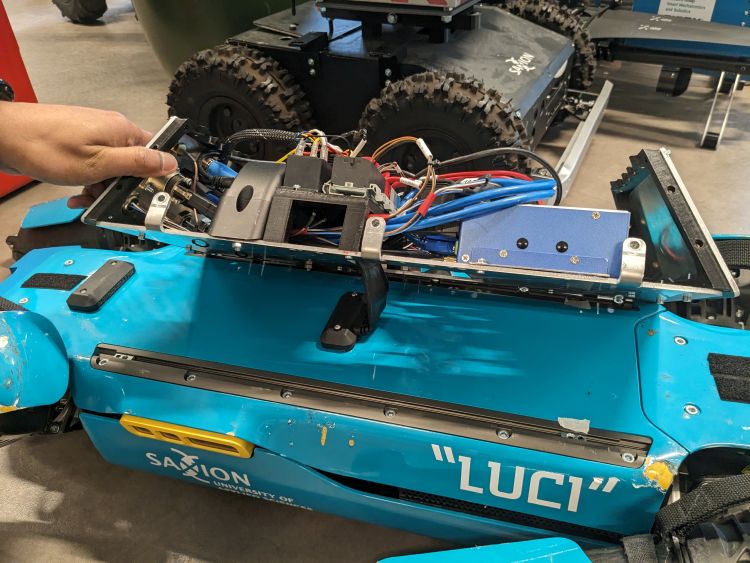
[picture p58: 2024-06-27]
Images/Assembly Instructions/connecting_GXP.jpg

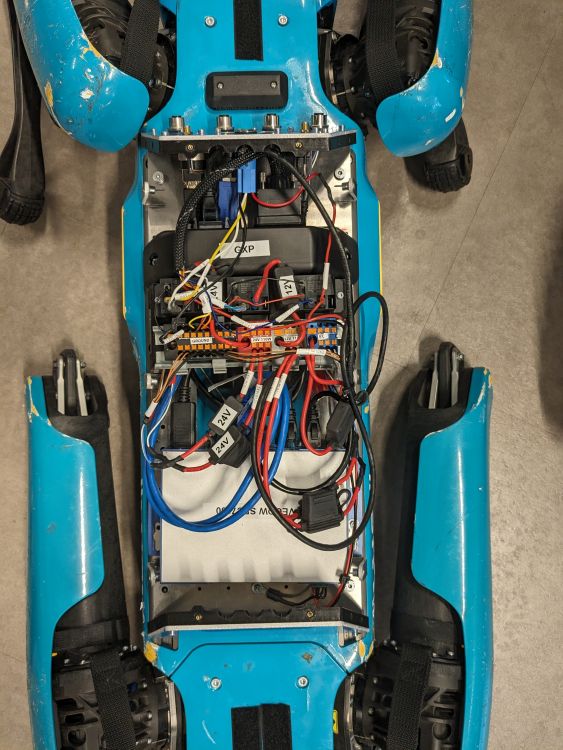
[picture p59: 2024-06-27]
Images/Assembly Instructions/mounted_mounting_plate2.jpg

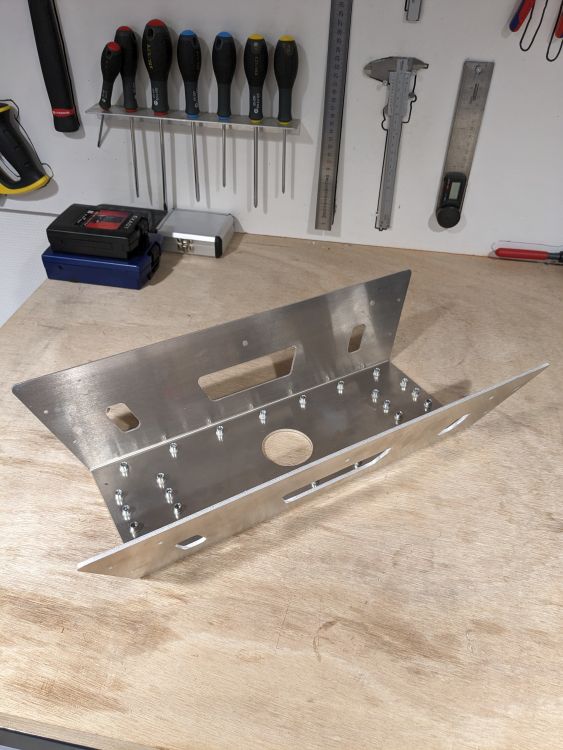
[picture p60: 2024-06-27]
Images/Assembly Instructions/rivets3.jpg

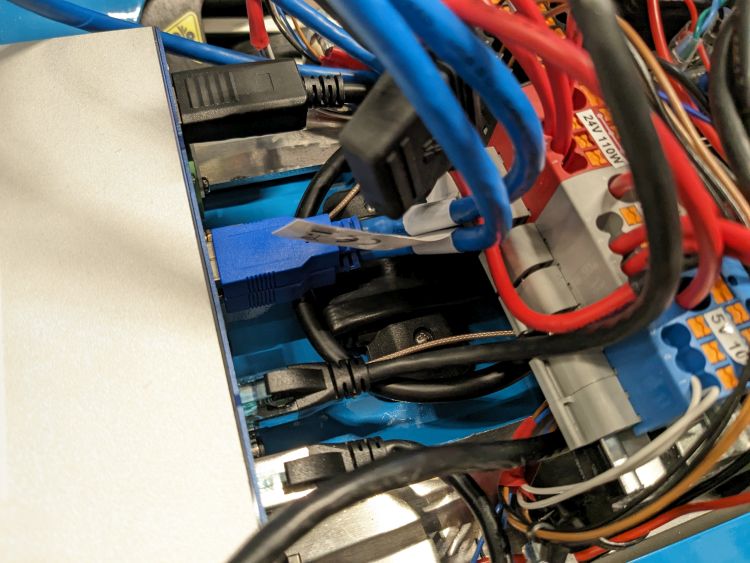
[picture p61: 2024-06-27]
Images/Assembly Instructions/internals3.jpg

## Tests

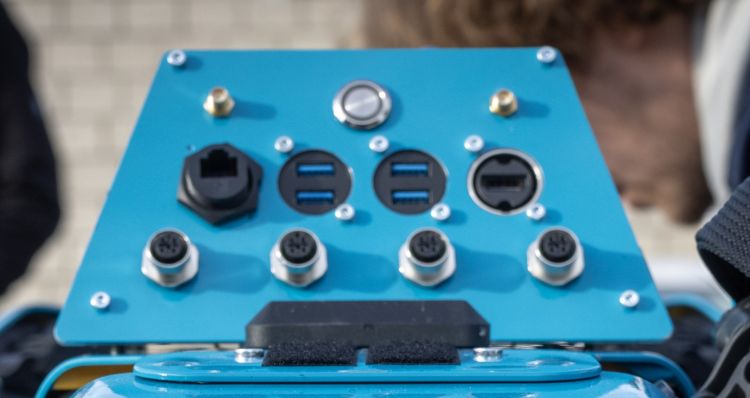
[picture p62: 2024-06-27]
Images/KIWA_Test_Day/panel_not_sharp.jpg

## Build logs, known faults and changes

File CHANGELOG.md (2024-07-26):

# Changelog

## 2.0.1
- Fix build warnings in `Backpack Assembly.SLDASM` `[4e51dbc]`
- Fixed typos in documentation `[fe46731]`
- Added grey background to diagrams in order to facilitate users who use dark theme in their browser or code editor `[f4e4705]`
- Used the SolidWorks `Pack and Go` method to reference to relative file paths instead of absolute ones `[c10bc23]`

## 2.0.0
- Remodelled the entire the design to mount the outer shell from the top onto the mounting plate in order to make the design more user friendly  `[3eeae9e]`. As such, 
  - Bends on the panels and the main mounting plate have been removed.
  - 3D printed brackets with heat inserts have been designed to mount the panels onto the mounting plate
  - Small bends with holes for rivet nuts have been added to the mounting plate   

- Simplified mounting pattern on top of the outer shell and added holes for rivet nuts to make mounting more user friendly `[fe60203]`
- Added a cable grommet to the top surface of the outer shell `[6a6446d]`.
  
- Added sheet metal braces to the GPS wings for stabilization `[e94383c]`
  
- Added WIFI antennas to the interface panel `[601d97e]`
- Replaced XT60 connectors with M12 connectors  [51b7a99]`
- Swapped the position of power and media connectors on the panel interface for better cable play `[040230a]`

- Added custom mount for the Laser Hunter gas sensor `[8efb5fd]`
- Added parts for power distribution `[6791d271]`

## 1.0.0
- First prototype version by Nick Older Rikkert

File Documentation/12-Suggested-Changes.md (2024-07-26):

## Suggested Changes

Below you can find a list of suggested changes:

* **Make the backpack easier to mount & use**
  * Use the 2nd interface bus of SPOT (the one in the back) for the GXP instead of the one in the center. For instance, add a cutout for the interface panel such that the main wire of the GXP can hang outside of the backpack or mount the GXP itself on the back of SPOT, outside of the backpack. This way we can do the following: 
    * Add screw holes on the mounting plate that extrude from the front and back panel, such that you can directly mount it on the rails on SPOT without having to remove the outer shell. 
  * Re-design the top of the outershell such that you can open it. For instance, it could be attached to the main frame as a lid and open like a "door", similar to a [control box](https://nl.rs-online.com/web/p/wall-boxes/7755798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). 
* Re-design the backpack to be IP54 (same as SPOT).
* Remove the screw holes on the sides of the outer shell for the panels, they are not needed.
* Remove the sheet metal bends in the middle of the main mounting plate, they are not needed. Remove the corresponding screw holes on the outer shell as well.
* Make the backpack larger, the current design is very cramped due to the wiring.
* Decrease tolerance of nut holes of GNSS wings.
* Improve the design of the GNSS wings, there are currently a lot of screws for such a simple part and it takes too much time to assemble.

***

> ⬅️ [Previous: Architecural Decision Records](./11-decision-log.md)

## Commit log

2023-11-03 Renamed files from Nicks design and restructured folder structure
    [GPS Sensor.SLDPRT, GPS mount.SLDPRT, HDMI.Socket.SLDPRT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]
2023-11-14 Added 3D printed bracket to avoid bends; added holes for wifi antennas
    [Bracket.SLDPRT, Mounting Plate.SLDPRT, Outer Shell.SLDPRT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]
2023-11-17 Added side bends to the mounting plate (compatible with Sophia)
    [Bracket.SLDPRT, Mounting Plate.SLDPRT, Outer Shell.SLDPRT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]
2023-11-23 Added cable clearance area to Vecow PC
    [Vecow spc-7000.SLDPRT]
2023-11-23 Made backpack 4mm wider to accomodate GXP
    [Bracket.SLDPRT, Outer Shell.SLDPRT, Panel Back.SLDPRT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]
2023-11-23 Moved middle finger bend to the actual middle and matched distance to the wider outer shell
    [Bracket.SLDPRT, Mounting Plate.SLDPRT, Outer Shell.SLDPRT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]
2023-11-23 Increased hole size for rivet nuts (Sophia compatible)
    [Mounting Plate.SLDPRT]
2023-11-23 Moved Antenna holes to other panel side
    [Panel Back.SLDPRT, Panel Front.SLDPRT]
2023-11-24 Added LaserHunter
    [Bracket.SLDPRT, LaserHunter.SLDPRT]
2023-11-27 Added new components, swapped panels around
    [3-D NE8FDY-C6.stp, 415300.stp.SLDPRT, Bracket.SLDPRT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]
2023-11-27 Simplified and adjusted mounting surface for rivet nuts
    [GPS mount.SLDPRT, Outer Shell.SLDPRT]
2023-11-27 Added revised LaserHunter mount
    [LaserHunterMount.SLDPRT]
2023-11-28 Added M12 Connectors and WiFi antennas
    [Antenna_assembly v4.step, Bracket.SLDPRT, M12-4pole-pxc_1401206_09_00_SACC-E-M12FS-4CON-PG9-1-0-VAPO_3D.stp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]
2023-11-29 Added GPS wing enforcements and relay
    [Bracket.SLDPRT, GPS mount enforcement v15.step, GPS mount.SLDPRT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]
2023-11-29 Made velcro strap holes more user friendly
    [LaserHunterMount.SLDPRT]
2023-11-29 Added cable grommet
    [Cable Grommet.SLDPRT, Outer Shell.SLDPRT]
2023-11-29 Added bents to LaserHunter mount (Sophia compatible-ish)
    [GPS mount.SLDPRT, LaserHunterMount.SLDPRT, Outer Shell.SLDPRT]
2023-11-29 Added DIN rail and ethernet switch
    [DIN-Rail-60mm.step, DIN-Rail-77mm.step, DIN-Rail-pxc_0801733_06_03_NS-35-7-5-PERF-2000MM_3D.stp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]
2023-11-29 Changed height of windows
    [LaserHunterMount.SLDPRT, Outer Shell.SLDPRT]
2023-11-30 Added more detailed GNSS sensors and corrected mounting holes
    [GPS mount.SLDPRT, H-RTK F9P GNSS CH7604A.SLDPRT, H-RTK F9P GNSS CH7604A.STEP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]
2023-12-01 Made holes d-shaped for antenna and M12 connectors
    [Panel Front.SLDPRT]
2023-12-07 Added new relays and cable grommet
    [51540_01.SLDPRT, 51540_02.SLDPRT, 51540_03.SLDPRT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]
2023-12-07 Added PWR DISTR mount
    [PWR DISTR Mount.SLDPRT]
2024-04-02 Last changes before KIWA test day
    [Bracket.STEP, PC_bracket.SLDPRT, heat_insert_test_print2.SLDPRT]
2024-04-05 fixed brackets, deleted not needed files
    [Bracket.SLDPRT, DIN-Rail-60mm.step, DIN-Rail-77mm.step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]
2024-04-05 Added screw holes for GPS wings
    [GPS mount.SLDPRT]
2024-04-05 Fixed D-shape antenna holes
    [Panel Front.SLDPRT]
2024-04-05 Remodelled PWR distr, added correct holes for PWR distr and GXP
    [Bracket.SLDPRT, DIN-Rail-pxc_0801733_06_03_NS-35-7-5-PERF-2000MM_3D.stp, DIN_rail.step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]
2024-04-05 Removed DIN rail, kept breaking everything
    [DIN_rail_new.step, PWR DISTR Mount.SLDPRT, ptfix_18_new.stp]
2024-04-05 Show components
    [Panel Back.SLDPRT]
2024-04-05 restructured locations of components
    [3-D NE8FDY-C6.stp, 415300.stp.SLDPRT, Antenna_assembly v4.step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]
2024-04-08 Started with assembly instructions
2024-04-15 Added draft version of assembly instructions (without images)
2024-04-22 Seperated mounting and assembly instructions
2024-04-23 Added screw lengths to assembly and mounting instructions
2024-05-13 Added Power Distribution
2024-05-14 Update assembly
    [Bracket.SLDPRT, Mounting Plate.SLDPRT, Panel Back.SLDPRT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]
2024-05-14 Restructured folder structure
    [3-D NE8FDY-C6.stp, 51540_01.SLDPRT, 51540_02.SLDPRT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]
2024-05-30 Updated Assembly instruction with electrical diagram
2024-06-03 Added parts list (STILL UNDER REVIEW)
    [parts_list.xlsx]
2024-06-27 Updated documentation for release
    [parts_list.xlsx]
2024-07-19 Used Pack and Go function to use relative instead of absolute paths
    [Bracket.SLDPRT, Cable Grommet.SLDASM, GPS mount.SLDPRT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]
2024-07-26 Fix build warnings
    [Bracket.SLDPRT, GPS mount.SLDPRT, LaserHunterMount.SLDPRT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]
